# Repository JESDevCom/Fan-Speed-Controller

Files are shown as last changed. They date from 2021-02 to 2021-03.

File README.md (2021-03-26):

# Fan-Speed-Controller

**Part I. Introduction**
   * Re-Engineering a YLFC700 Fan Speed Controller (TRIAC based). This controller was originally sourced from an Xtrodinair Apex 42 Fireplace. The problem with the controller is that the slide potentiometer fails over time (about every 2-years). It fails at the slider's position where the fan runs just below max speed. 

**Part II. Theory for Failure**
   * The potentiometer is rated for 100[mW].
   * The reason the potentiometer fails is because the 47 [nF] Film capacitor begins to fail from transient voltage spikes after many startups.
   
**Part III. Testing Equipment Used**
1. Fluke 87V Digital Multimeter
2. Siglent SDS 1104X-E 100MHz Oscilloscope
3. Krohn-Hite Model 1600 3MHz Frequency Generator
4. Generic 5[V] 1[A] Fixed Power Supply
5. Hakko Soldering Station
6. Quick Hot Air Soldering Station

**Part IV. Software Used**
1. Windows 10 Pro
2. KiCAD 5.1
3. Matlab

**Part V. Parts Used**
1. RV1, 91A1A-B28-A22L, 0.2 [Ohms] to 250 [kOhms] Linear Potentiometer, Turn Knob Style, 2[W] max.
2. R1, 2.4k, Reused
3. R2, 270k, (Min: 0.25[W], Bought: 0.5[W])
4. R3, 18k,  (Min: 0.25[W], Bought: 0.5[W])
5. R4, 240k, (Min: 0.25[W], Bought: 0.5[W])
6. R5, 24, (Bought: 1[W])
7. U1, BTA16-600B, TRIAC (non-insulated tab package)
8. U2, DB3, DIAC (15 [uA] breakover current is my guess).
9. C3, 100 [nF], Film Capacitor 250[Vdc]
10. C2, 100[nF], Film Capacitor 250[Vdc]
11. C1, 47[nF], Ceramic Capacitor 1 [kVdc] (X7R)
12. L1, Inductor 7[uH] @ 1[KHz] (Measured with Scope, see characterization plot in Matlab folder)
13. 1/4" Dia. Metal Knob for Potentiometer

**Part VI. LTspice Simulation**
   * As the 47 [nF] fails, the potentiometer begins to seriously fall out of spec. 
   * Note, that the Power Factor (PF) is approximately 86% in the potentiometer resistance range where the slider fails (100 to 30k).

**Part VII. KiCAD Schematic**
   * Since this Controller adjusts the blower's speed on the fireplace and this motor is rated for 1.8 [A], let's design the PCB for double the max operating current because we can :). 
   * The only added components from the original design:
      1. 4 [A] fuse will be added, 
      2. a 24 [Ohm] resistor will be added in series with the potentionmeter since the potentiometer's minimum resistance is 0.2 [Ohms],
      3. a toggle switch to disconnect the controller from the 120 Volt mains to recreated the off detent that was on the original board, 
      4. and my design will not have any exposed PCB traces from the Fab.
      
   * We will reuse:
      1. 2.4k through-hole resistor,
      2. the two 100 [nF] film capacitors, 
      3. TRIAC, 
      4. DIAC, 
      5. and Inductor since these reactive components were engineered for use in the original design.

   * We will replace:
      1. 18k through-hole with a 18k in a 1206 package,
      2. 240k through-hole with a 240k in a 1206 package,
      3. 270k through-hole with a 270k in a 1206 package,
      4. the no-name slide potentiometer with a Bourns 91A1A-B28-A22L Knob Potentiometer,
      5. 47 [nF] 400 [Vdc] Radial Film Capacitor with a 47 [nF] 1 [kVdc] (X7R) Radial Ceramic Capacitor
     
   * A Bourns 91A1A-B28-A22L Knob Potentiometer (2[W], 0.2 to 250k [Ohms], linear) will repalce the original slide potentiometer (100[mW], 30 to 300k [Ohms], log). Since this potentiometer is in parallel with two other resistors, a 240k and 296k [ohms], the max resistance of the potentiometer doesn't matter that much. However, the minimum reistance does matter because it greatly affects the max speed (ie, the potentiometer controls the rate that the capacitors charge, which controls how the 120 [Vac] sinewave is chopped; thereby, changing the fan speed. marvelous).
   * Since the potentiometer goes down to 0.2 [Ohms], an excessive amount of current is drawn across the potentiometer, so a 24 Ohm resistor will be added in series with the potentiometer to approximately match the original slide potentiometer's minimum resistance. 
  
 **Part VIII. KiCAD PCB Design**
   * A two-side PCB will be created and fabricated, I used OSHpark as the frabricator.
   * SMD resistors for the 18k, 240k, 270k, 24 Ohm Resistors are required to make space for the Knob Potentiometer.
   * Certain traces that follow from the VAC input, to the TRIAC, and out to the motor must be fat traces (4mm) to stay below current and heat limits of having covered traces.
   * 0.2mm minimum distance between traces is important for 120[Vac] designs.

**Part IX. Disassembly of Original Boar & Removal of Components**
   * Remove the plastic & copper PCB mounting stands that connect the PCB to the metal outlet mount.
   * Use a Soldering Iron or Hot Air Station to remove the inductor, DIAC, TRIAC, and Capacitors.
   * Check capacitors with Fluke 87V.
   * Resolder the new and old components to the new board. 

**Part X. Results**
   * When removing the capacitors from the original board, the 47 [nF] Film Capacitor was measured at 1.2 [nF]. The 100 [nF] film capacitors were still in 10% spec.
   * After simulating the LTspice model with such a value (1.0nF) it became clear that the reason the potentiometer failed was because the 47 [nF] capacitor failed. This 47 [nF] capacitor is marked C1 on the original board (YLFC700).
   * Reason for failure: the capacitor is configured as a snubber and there is likely overvoltage spikes due to the motor.
   * Solution: Use a cermaic capacitor that has a higher maximum voltage rating that can withstand spikes resulting from the TRIAC switching. 
   
   * Successfully operating as of March 2021.

**Part XI. Legal Notice**
 
Under the MIT license to this project, you may use this design freely. An email to alledgedlyengineering @ gmail stating that you used this design would be nice to know. By using this project you are agreeing to the risks involved with AC current and altering a UL listed product to fit your needs. In addition, you agree to not hold me responsible for any injury or result of injury incurred by modifying the YLFC700 Fan Speed Controller. This project has no affliations with any of the manufacturers used in this design or the PCB fabrication house used.

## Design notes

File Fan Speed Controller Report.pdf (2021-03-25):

# YLFC700 Fan Speed Controller Product Failure & Solutions

## March 26, 2021

## John Schulz

# Table of Contents

Table of Contents | 1
Introduction | 3
Signs of Failure | 3
Theory for Failure | 3
Theoretical Design Flaws | 4
Specifications | 4
AC Motor | 4
YLFC700 | 5
Product Image | 5
Component List | 6
Fan Speed Controller (FSC) | 7
Component List | 7
Equipment Used | 8
Hardware | 8
Software | 8
Procedure | 8
Design | 9
YLFC700 | 9
Measured Inductor Characteristics | 11
LTspice Schematic | 11
Schematic Operation | 13
LTSpice Simulation | 13
Testing | 15
Transient Over Voltage | 15
Capacitor Measurements | 16
Solutions | 16
Fixing A New YLFC700 | 16
Engineering A Fan Speed Controller | 17
KiCAD Schematic | 17
KiCAD PCB Design | 18
Results | 21
Conclusion | 23
Appendix I - Code | 24

Inductor Characterization.m | 24
Power Factor.m | 28
LTspice Netlist | 29
Appendix II - Packaging | 32

# Introduction

The TRIAC-based fan speed controller used in an Xtrordinair Apex 42 fireplace has the model number: YLFC700. This unit is likely sourced by Travis Industries from an unknown supplier that produces the YLFC700. The fan speed controller is designed to control the speed of a single-pole 120V AC motor at a maximum AC current of 5A.

I own two units of the YLFC700, all of which have failed in the same manner. The problem with the controller is that the slide potentiometer partially fails over time, within 2 to 3 years, causing a specific range of usage on the potentiometer to no longer control the motor’s speed. To fix this problem I created my own personal hobbyist fan speed controller. I will call this version Fan Speed Controller (FSC) for the remainder of this document.

# Signs of Failure

Unfortunately, there are not any obvious signs that the unit begins to fail internally. The first external sign that the operator will notice is arcing across the contacts inside the slide potentiometer used in the YLFC700. The next sign of internal failure is when the contacts on the potentiometer become burnt out enough that contact can no longer be made and the motor stops operating in that position on the slide potentiometer. The slide range on the two YLFC700 units fail:
1. just below max speed (max speed still works) and
2. just above the halfway point on the slider.

# Theory for Failure

The potentiometer is likely rated to withstand 100mW of power. When a 120V AC current is applied and the controller is initially turned on, the potentiometer is its lowest resistance range which correlates to operating the motor at max speed. At this point, the transient state of the controller is affected by the inrush of current and a back EMF voltage spike from the motor initially receiving power from the controller. Inside the YLFC700, this transient voltage spike harms the 47nF 400V Film Capacitor C1, which in turn causes the 100mW potentiometer to fail as it is the next weakest link.

The reason capacitor C1 fails slowly is because a film capacitor is used and most film capacitors are self-healing. Since the transient condition that causes the failure only occurs at startup, the capacitor self-heals under normal operation; however, the self-healing characteristics degrade after each transient shock occurs. The reason the slide potentiometer only fails in the faster fan speed range of the controller is that this is the range of highest wattage consumed by the potentiometer.

# Theoretical Design Flaws

1. The YLFC700 does not use a snubberless TRIAC, yet the product was designed without a true snubber configuration being a resistor in series with C1. Due to the nature of the load (AC motor), the device should use a snubber to absorb the harsh opening and closing nature of the TRIAC.
2. Since the YLFC700 is designed to control motors, overvoltage transient protection using a TVS diode should probably be employed.
3. Depending on the load, a higher voltage-rated C1 capacitor may be a solution.
4. To reduce transient current inrush when the YLFC700 is turned on and connected to the AC motor, the slide potentiometer should be flipped 180 degrees to start the motor at its lowest speed instead of its highest speed.

# Specifications

The following specifications cover the motor that the YLFC700 is connected to, the components inside the YLFC700, and the components used in my hobbyist fan speed controller.

## AC Motor

Manufacturer: Fasco
Model Number (Type): U73B1 Voltage: 120V AC @ 60Hz
Current: 1.8A
Speed: 1550 RPM

In testing, the motor operated just below 1.8A when set at its max speed by the YLFC700 controller. This is normal and the motor ran as expected.

## YLFC700

### Product Image

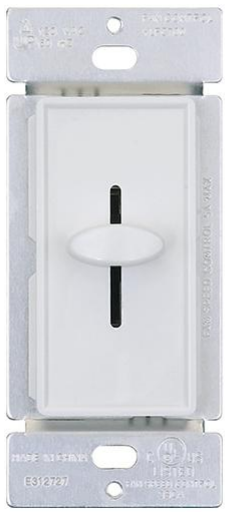
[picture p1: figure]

Figure 1 - YLFC700 OEM Product Image

The image in figure 1 displays the YLFC700 fan speed controller that is used in Travis Industries Apex 42 fireplace controller.

### Component List

Table 1 contains the list of components found inside the YLFC700 fan speed controller and the replacement components used in my hobbyist version.

Table 1 - YLFC700 Components
Original Components | Replacement Components (Hobbyist Version)
Slide Potentiometer, 20mm, 20-300k Ohms Logarithmic, 100mW | Rotary Potentiometer: RV1, 0.2-250k Ohms Linear, 2W
Resistor, 2.4k, Wattage NA | Resistor: R1, 2.4k*
Resistor, 270k, Wattage NA | Resistor: R2, 270k, 0.5 W
Resistor, 18k, Wattage NA | Resistor: R3, 18k, 0.5W
Resistor, 240k, Wattage NA | Resistor: R4, 240k, 0.5W
Film Capacitor: C1, 47nF, 400V | Ceramic Capacitor: C1, 47nF, 1kVdc (X7R)
Film Capacitor: C2, 100nF, 250V | Film Capacitor: C2, 100nF, 250V*
Film Capacitor: C3, 100nF, 250V | Film Capacitor: C3, 100nF, 250V*
TRIAC, BTA16-600B, non-insulated tab | TRIAC: U1, BTA16-600B, non-insulated tab*
DIAC, DB3, Breakdown Current NA | DIAC: D1, DB3, Breakdown Current NA*
Inductor: L1, Syle: Radial Vertical, Inductance Rating: Unknown, Measured at 7uH @ 1kHz | Reused Original Part*

* Components reused from the original PCB and resoldered to the new PCB board I created.

## Fan Speed Controller (FSC)

### Component List

Table 2 contains a list of components I used in my hobbyist version.

Table 2 - Fan Speed Controller v1.0 Components
Rotary Potentiometer: RV1, 0.2-250k Ohms Linear, 2W **

Resistor: R1, 2.4k *

Resistor: R2, 270k, 0.5 W **

Resistor: R3, 18k, 0.5W **

Resistor: R4, 240k, 0.5W **

Resistor: R5, 24, 1W ***

Ceramic Capacitor: C1, 47nF, 1kVdc (X7R) **

Film Capacitor: C2, 100nF, 250V *

Film Capacitor: C3, 100nF, 250V *

TRIAC: U1, BTA16-600B non-insulated, Style: Through-Hole *

DIAC: D1, DB3, Style: Through-Hole, Breakdown Current NA *

Inductor: L1, Style: Radial Verticle, Inductance Rating: Unknown, Measured at 7uH @ 1kHz *

¼” Dia. Metal Knob for Potentiometer ***

Fuse: F1, 4A Fast Blow. ***

* Components reused from the original PCB and resoldered to the new PCB board I created. ** Components different from the YLFC700 but serve the same purpose.
*** Components added to the circuit that was not in the YLFC700 circuit.

# Equipment Used

## Hardware

- Fluke 87V Digital Multimeter
- Siglent SDS 1104X-E 100MHz 4Ch Oscilloscope
- Krohn-Hite Model 1600 3MHz Frequency Generator
- Generic 5[V] 1[A] Fixed Power Supply
- Hakko Soldering Station
- Quick Hot Air Soldering Station

## Software

- Windows 10
- KiCAD 5.1
- Matlab 2017

# Procedure

The following steps are the procedure followed when re-engineering the YLFC700 while searching for the probable cause of failure.

1. Use the original PCB inside the YLFC700 to draw the schematic out in LTspice
2. Check resistor and capacitor values with Fluke 87V
3. Measure the inductor value with a frequency generator and Siglent oscilloscope
4. Record inductor values in Matlab and plot inductor characteristic curves
5. Calculate the power factor of the LTspice circuit to check if the potentiometer is within power spec
6. Draw schematic in KiCAD
7. Design PCB in KiCAD
8. Send PCB design to OSHpark for fabrication
9. Transfers reusable components from YLFC700 to FSC
10. Test motor with FSC and AC power source

# Design

## YLFC700

The construction of the YLFC700 PCB is a one-sided board that uses all through-hole mounted components.

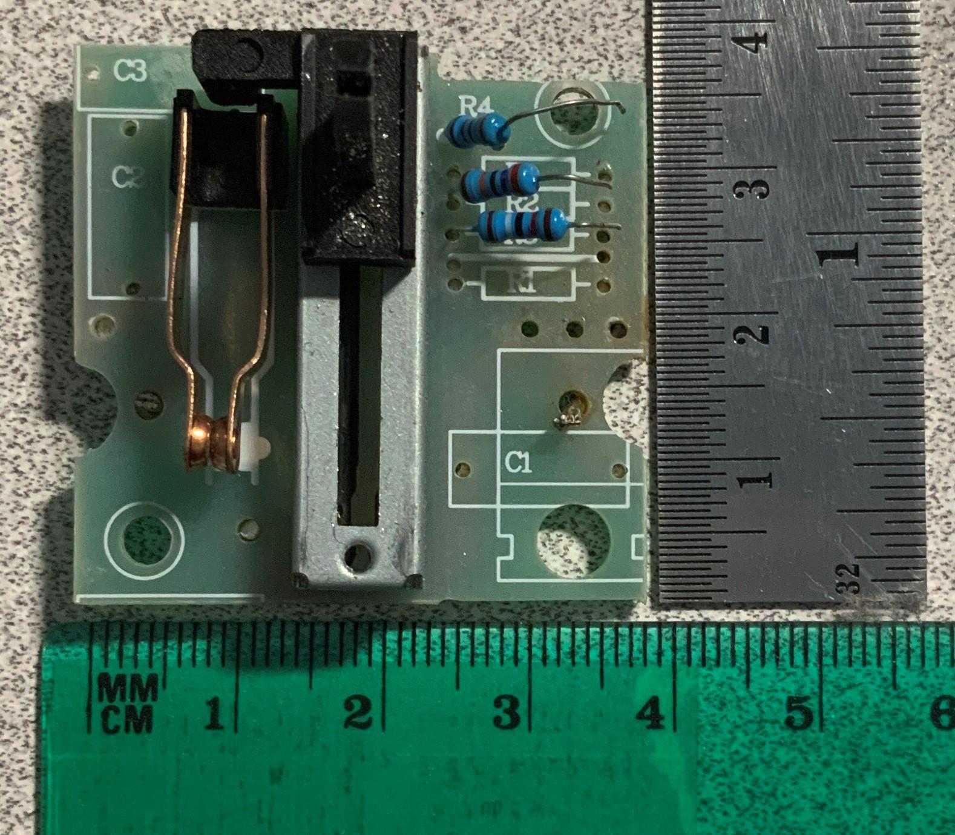
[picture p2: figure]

Figure 2 - YLFC700 PCB Front Side View

Figure 2 depicts an image of the PCB’s front side. This is the side of the board that faces the user when operating the fan controller. Some components have been removed from the board for the purpose of measuring their values. The removed components are as followed: C1, C2, C3, L1, TRIAC, DIAC, and R1. The dimensions of the PCB are 38mm along the translucent green ruler and 37mm along the metal silver ruler.

The long component located in the center of the board is the logarithmic slide potentiometer. The potentiometer has a slide distance of 20mm, a knob height of 20 mm, and dimensions of 35mm x 8.3mm x 6mm (L x W x H). The potentiometer is mounted to the board by 4 through-hole pins, two of which are necessary for operation. The pitch between the potentiometer’s pins is 3.5mm. Through research, I think this potentiometer is made by Panasonic and is rated for 100mW. Unfortunately, Panasonic no longer produces this exact potentiometer.

Next, the copper clip to the left of the slider is the power disconnect switch. The user feels this switch as a detent when turning off the controller.

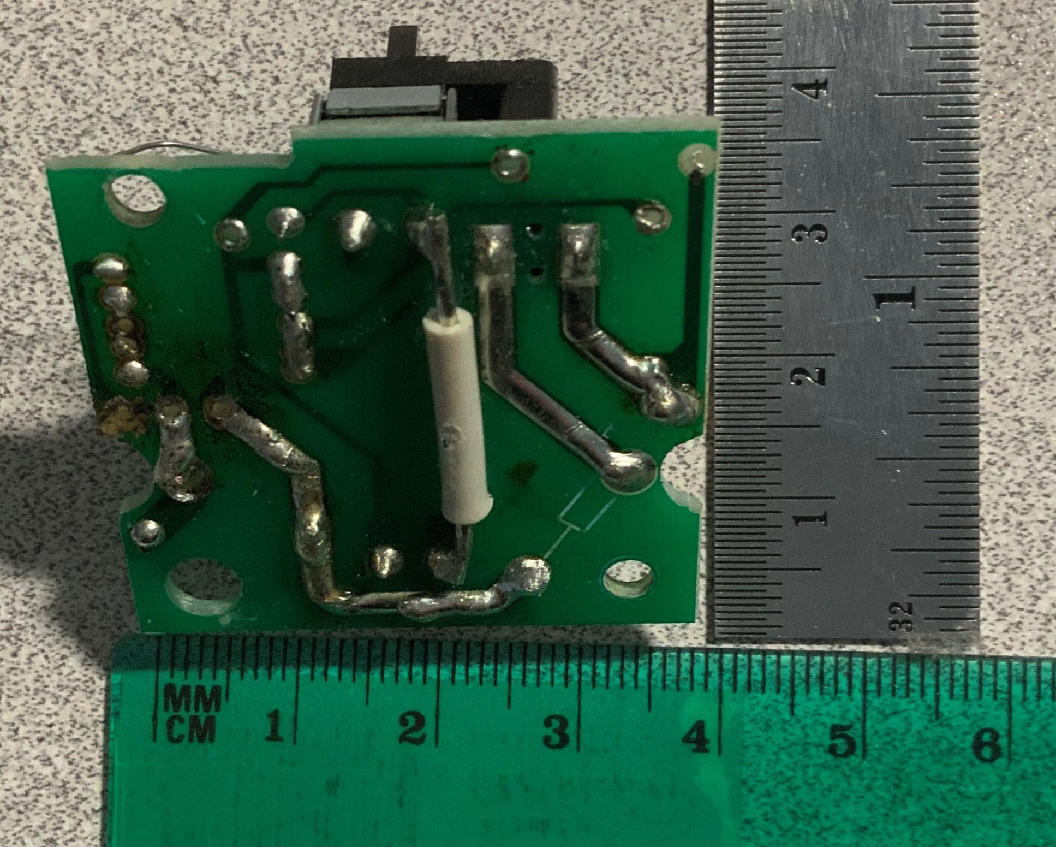
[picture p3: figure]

Figure 3 - YLFC700 PCB Back Side View

Figure 3 shows a view of the backside of the board, which is the side of the board that faces the wall when the user is operating the fan controller. Open traces were used along the main power route from the mains power side through the inductor, TRIAC, and out to the motor. Using exposed traces is a cheap way to carry a lot of current while dissipating heat. The black ABS plastic shielding that covers the PCB on the backside of the YLFC700 is required to shield the open traces.

### Measured Inductor Characteristics

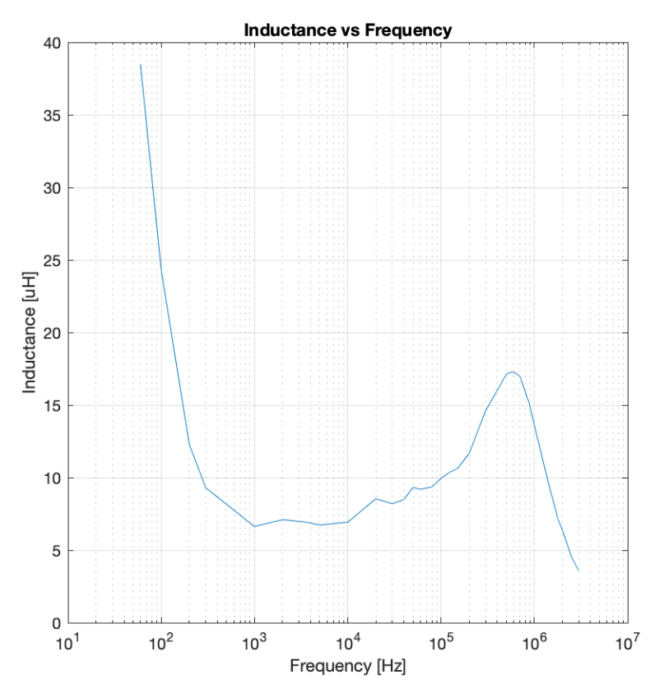
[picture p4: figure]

Figure 4 - Inductor (L1) Inductance vs Frequency

The inductor characteristics, shown in figure 4, used data collected and saved in a Matlab script to plot the above inductance versus frequency curve. The first point in the plot was collected at 60 Hz, which is the frequency the inductor will be operating at inside the YLFC700. Hence, an inductance value of 37uH will be used in the following LTspice simulations. See Appendix I, for the full Matlab characterization script with data.

### LTspice Schematic

After measuring the discrete components and sketching the PCB traces, the following schematic was created in LTspice. To simplify simulating an AC motor, an inductor in series with a resistor was implemented. It is my assumption that the motor would be relatively close to the value of the inductor L1 so 47uH was chosen. Secondly, the resistor value for R6 was chosen such that the motor would draw 1.8A when the potentiometer is set to operate the motor at max RPM. Note, all simulations use a 120V 60Hz sine wave input.

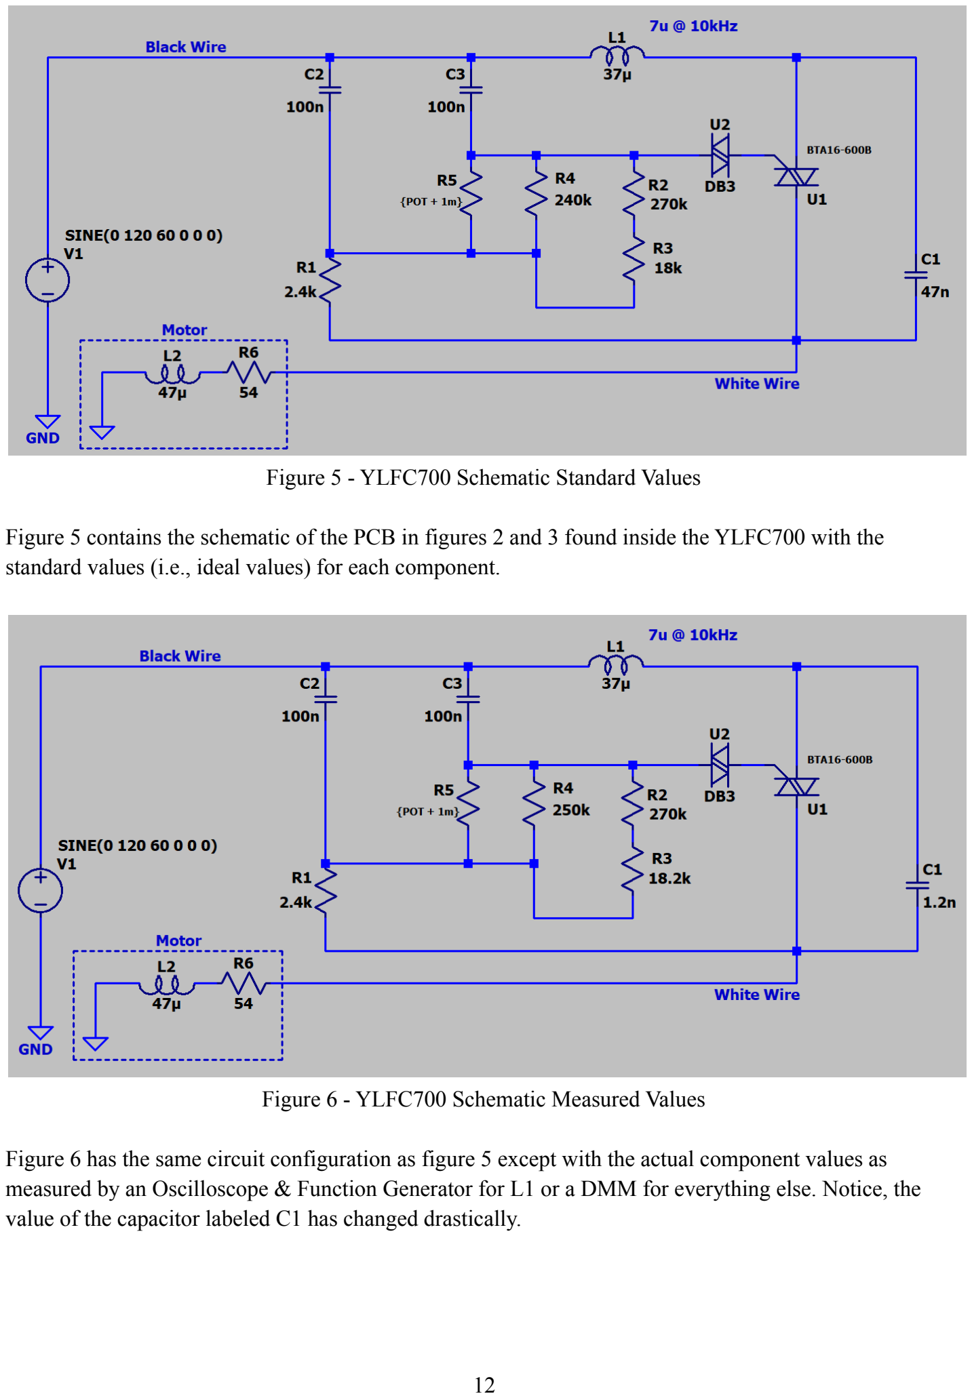
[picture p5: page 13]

Figure 5 - YLFC700 Schematic Standard Values

Figure 5 contains the schematic of the PCB in figures 2 and 3 found inside the YLFC700 with the standard values (i.e., ideal values) for each component.

Figure 6 - YLFC700 Schematic Measured Values

Figure 6 has the same circuit configuration as figure 5 except with the actual component values as measured by an Oscilloscope & Function Generator for L1 or a DMM for everything else. Notice, the value of the capacitor labeled C1 has changed drastically.

### Schematic Operation

To break down the operation of the circuit from the schematic in figures 5 and 6, let's first discuss the DIAC and TRIAC (labeled U2 and U1). Under normal operation, the TRIAC opens and closes allowing current to flow through when a specific voltage is met at its gate. The DIAC controls the TRAIC’s gate. The DIAC turns on allowing current to flow through once a specific breakdown current occurs inside the DIAC. This breakdown current event can only occur once the capacitors C2 and C3 are charged. Hence by adjusting the rate at which C2 and C3 charge using the resistor network R1-5, the user can control DIAC.

The RPM of the AC motor is controlled by chopping the sine wave input; whereby, the motor does not see the full length of the sine wave over each period which manipulates the speed. The inductor L1 operates as an inductive line choke to keep the noise from the motor out of the mains. L1 and C1 are used to absorb the voltage spike caused by the motor when the TRIAC closes. Also, the capacitor C1 is used to fill the load when the TRIAC first opens; thereby, reducing the inrush current pulled from the mains.

Note, that if a resistor had been placed in series with C1, this part of the circuit would be a true snubber configuration.

### LTSpice Simulation

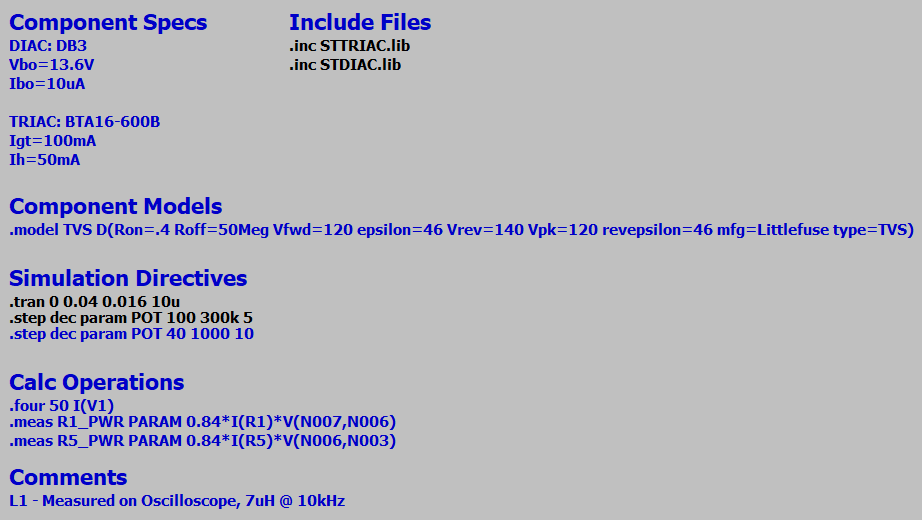
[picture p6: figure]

Figure 7 - LTspice Operations

The Spice operations used to simulate figures 5 through 6 are shown above in figure 7. Since the exact spice libraries for the DIAC and TRIAC used in the YLFC700 do not come with LTspice, one must download the files from STMicroelectronics and tell LTspice to include them. The circuits are simulated from 16ms to 40ms with a maximum timestep of 10us. The circuit has reached steady-state by 16ms. For each time simulation, a different potentiometer value is used in a logarithmic step from 100 Ohms to 300 kOhms with 5 points per decade.

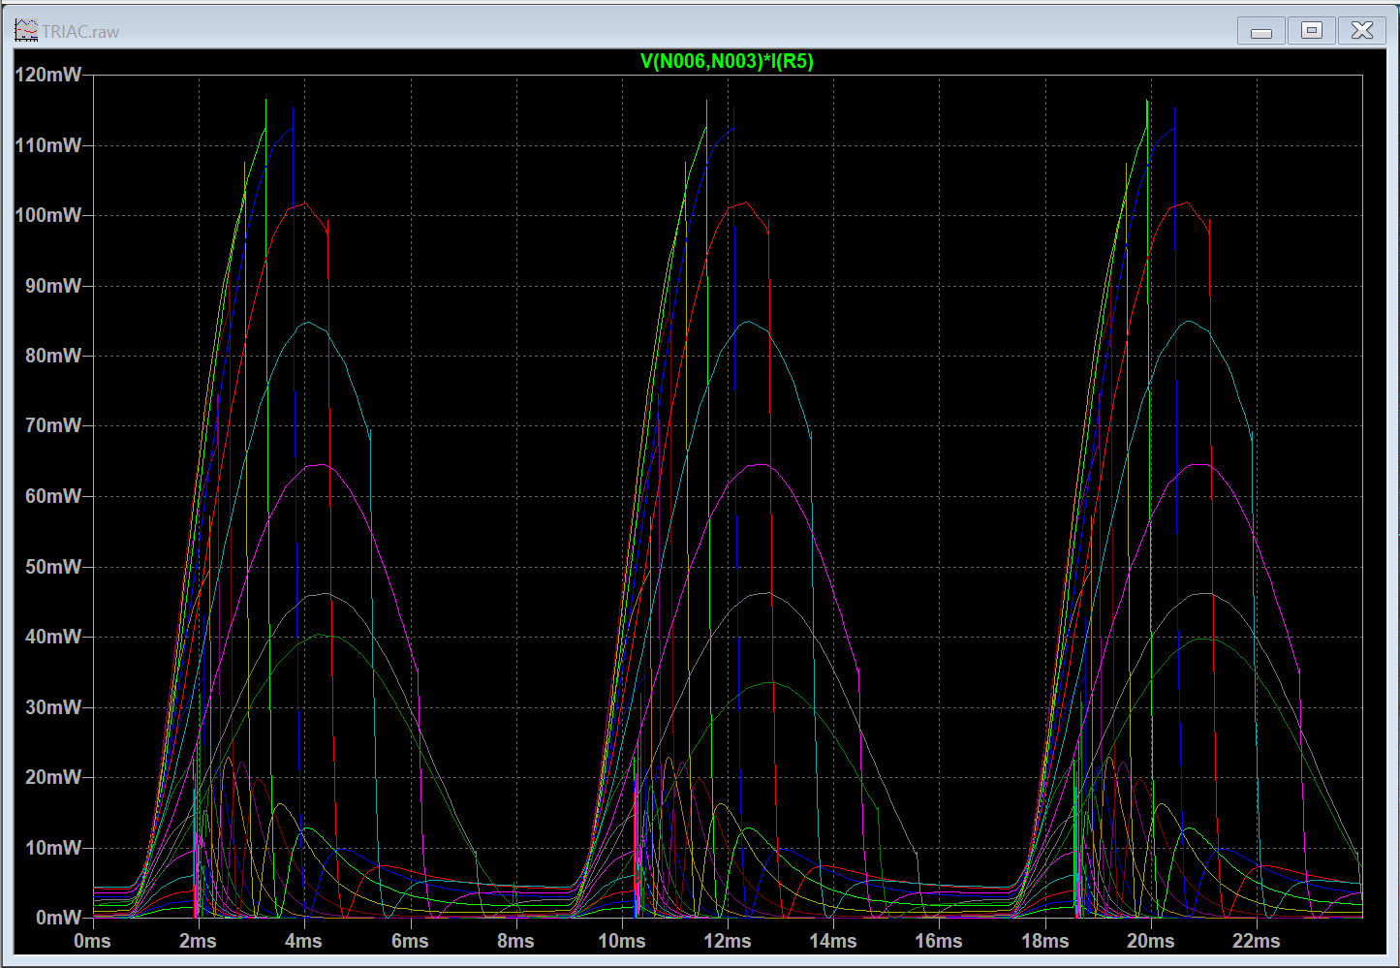
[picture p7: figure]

Figure 8 - Potentiometer Power Using Standard Values

To produce the simulation shown in figure 8, the circuit in figure 5 (actual values) and the operations in figure 7 are applied. When considering a power factor of approximately 86% for the potentiometer’s resistance values between 100 and 30,000 Ohms, the above results would be within specification. See Appendix I, for the Matlab script containing the power factor data collected from running the .four 50 I(V1) command in LTspice.

So, what happens when C1 starts to fail?

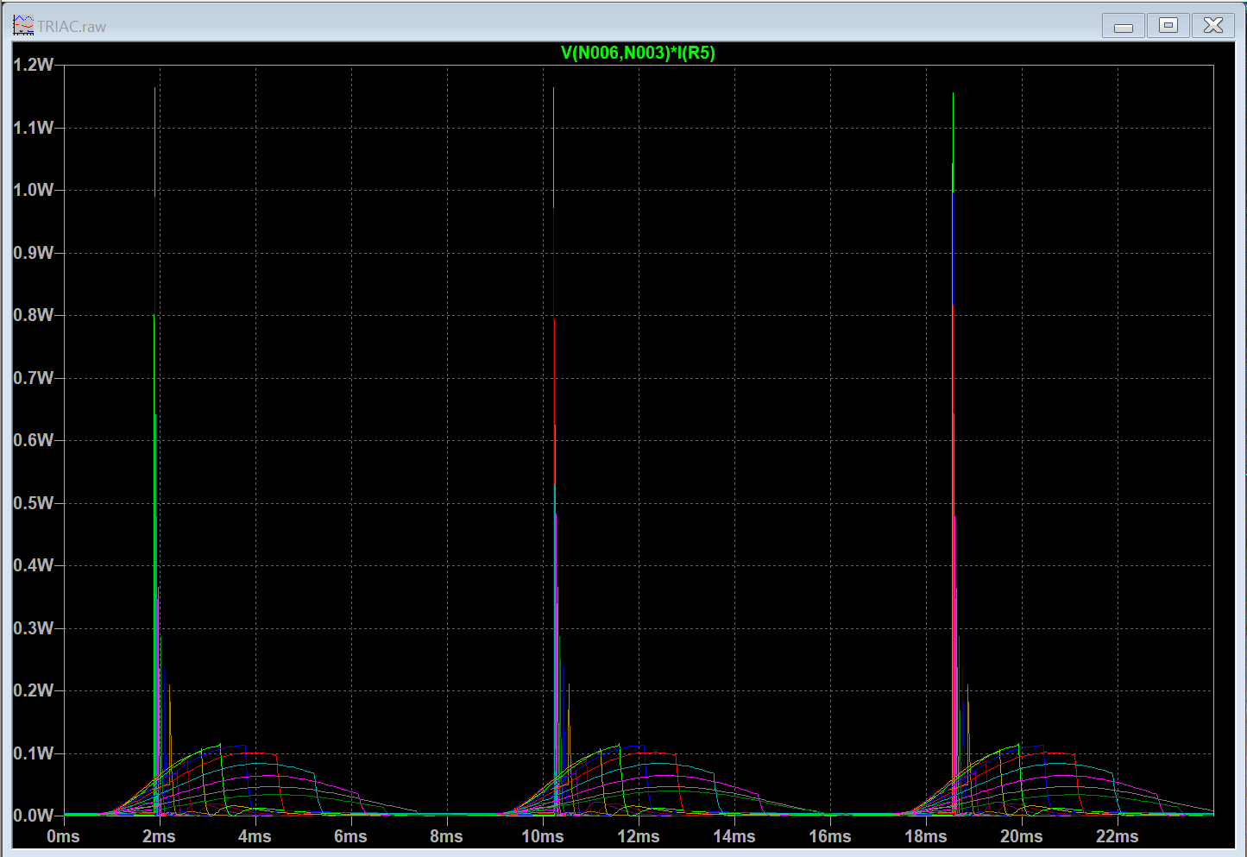
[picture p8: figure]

Figure 9 - Potentiometer Power Using Measured Values

To produce the simulation shown in figure 9, the circuit in figure 6 (measured values) and the operations in figure 7 are applied. Now one can see that when C1 fails and its capacitance decreases, the potentiometer falls dramatically out of specification over a range of resistance values from 100 to 30,000 Ohms. Hence, this is why the potentiometer inside the YLFC700 fails only in the upper-speed range, while the lower-speed control range remains functional.

# Testing

## Transient Over Voltage

During testing of the YLFC700 design, a transient voltage spike was seen when turning the unit on. I made an error in using my Oscilloscope without a high voltage differential probe. I was rather scared that I had ruined something inside my scope and I forgot to take a screenshot of the transient voltage spike. My probes were set at x10, my scope has a max peak to peak voltage of 400V, and my vertical V/div was set at the scope’s maximum. Under these conditions, I was unable to see the peak of the spike and I had my trigger set at 200V; therefore, I am assuming that the spike is around 400 volts or greater. Hence, the conditions would be met for the 400V rated capacitor to fail slowly.

## Capacitor Measurements

Capacitor C1 was measured before and after removal from the PCB. For both measurements, C1 was measured to be 1.2nF. Capacitors C2 & C3 were measured at 100nF.

# Solutions

There are two approaches to fixing the design flaws of the YLFC700:
1. Fix a brand new YLFC700 unit, or
2. Build a new fan speed controller.

## Fixing A New YLFC700

To fix a brand new YLFC700, place a Transient Voltage Suppression (TVS) diode on the right side of the circuit in parallel with C1, as seen in the figure below. This addition will protect C1 from the transient voltage spike cause when starting the motor.

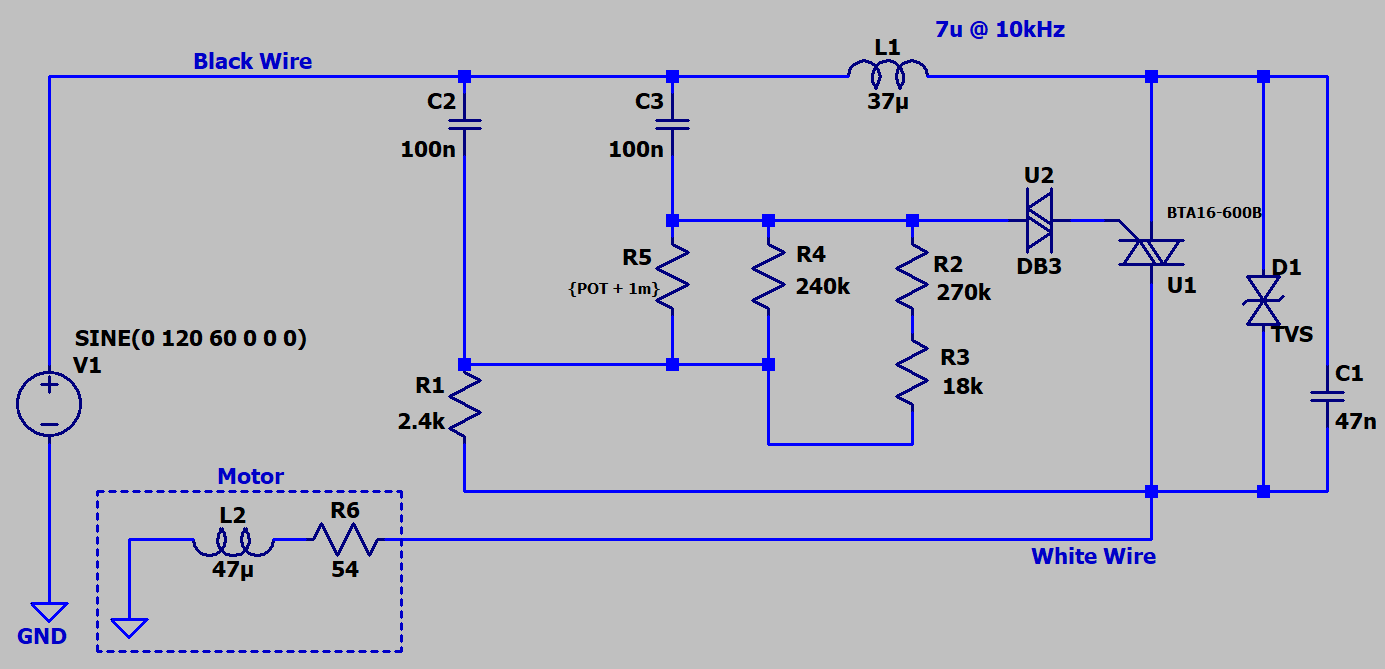
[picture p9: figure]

Figure 10 - Adding Transient Voltage Protection

A TVS diode such as the 5KP220CA by Littlefuse would be a good component for this problem since it will keep C1 from seeing a voltage greater than +/- 371V. Luckily, there is room to add a TVS diode to the YLFC700.

## Engineering A Fan Speed Controller

There are a few design considerations I made when re-engineering the circuit.
1. We want to reuse the original TRIAC mounted to the metal installation wall bracket along with the black ABS plastic cover used on the YLFC700; therefore, our new circuit board must fit inside the existing housing. See figure 17 as an example.
2. We may want to add a heftier wattage potentiometer than necessary. Slide potentiometers do not exist in a 2W package under our design constraints, so a rotary potentiometer will be used. A resistor (R5) must be added in series with the potentiometer to match the minimum resistance of the original slide potentiometer. This is necessary for the potentiometer chosen for our design because its minimum resistance is 0.2 Ohms.
3. A toggle switch (SW1) will be added to emulate the detent in the YLFC700 to disconnect the controller from the mains.
4. It never hurts to add a fuse, so a 4 Amp fuse will be added.
5. A 1kV ceramic capacitor will be used to replace the 400V film capacitor (C1). The ceramic cap will be much smaller than the film capacitor and it will fit better in the design.

Note: A film capacitor would still fit. Ceramic capacitors do not have self-healing properties like film capacitors; however, since our 600V rated TRIAC is not failing, I am assuming that a 1000V capacitor will survive.

### KiCAD Schematic

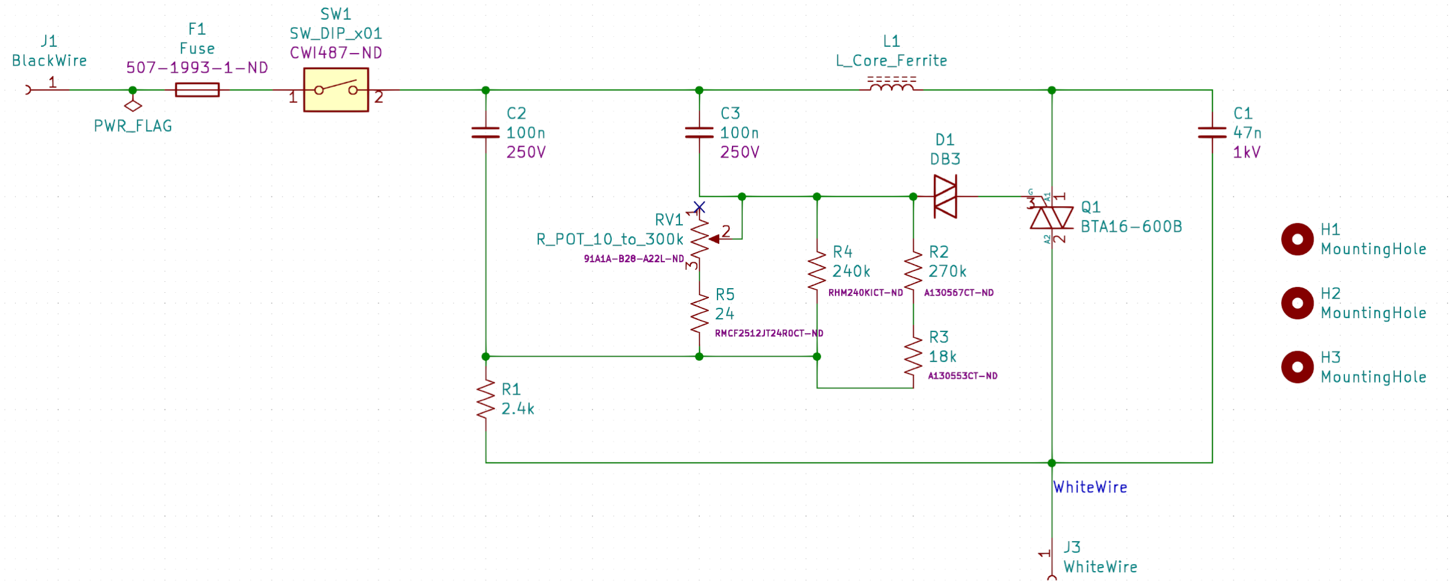
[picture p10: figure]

Figure 11 - KiCAD Schematic

Figure 11 shows the modified circuit that is used in my Fan Speed Controller design. The wire colors used on the YLFC700 correspond to the labels used in the above schematic. Notice, the original PCB had 3 mounting holes that were of different sizes and not connected to any traces on the board.

### KiCAD PCB Design

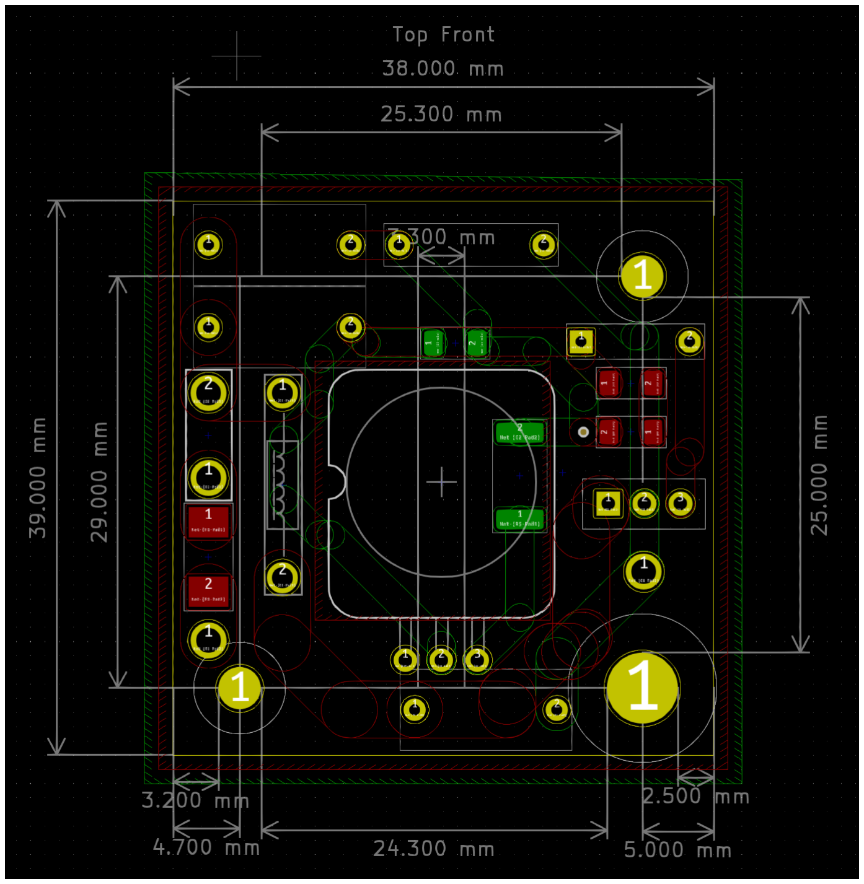
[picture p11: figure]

Figure 12 - KiCAD Design

Figure 12 shows the dimensions and spacing of components on the board. The diameter of the mounting holes and spacing between the mounting holes is critical if we want to reuse the existing YLFC700 mounting bracket and ABS plastic back cover. To add additional room for components, the height of the board increased by 2mm along its y-axis.

The yellow outline around the board marks the cut line that the fabricator will follow when they CNC our board. The red and green outline around the yellow cut line marks where the soldering mask will be poured. These two red and green boxes can be arbitrarily set anywhere outside the yellow cut line. Note, that the solder mask will be excluded from the top red layer, behind the potentiometer. This extra measure was implemented in the event that the potentiometer wiggles and wears on the PCB face to keep the potentiometer from ever touching the top layer traces. This should never occur under normal circumstances, but at the time of the KiCAD design, I didn’t know how snuggly the unit would go together.

Different trace widths were used in various areas of the design. By my estimation, the exposed traces on the original YLFC700 PCB were meant to handle a sustained 16A along the main route from the power input to the motor. However, we know our load uses a max 1.8AAC.

Using the Track Width PCB calculator in KiCAD, and knowing our fabricator will be OSHpark which uses a trace thickness of 0.0356mm, we can calculate the necessary trace thickness to handle the currents we expect using the IPC 2221 standard.

Thus, a 4mm wide internal trace with a temperature rise of 80C will allow the circuit to handle a max current of 8.25A along the main power trace from the 120V AC power input to the load. Similarly, a 2mm wide internal trace will handle 5A. This design uses either 4mm or 2mm traces because it is better to have extra thermal dissipation overhead than less. Considering the high voltage within this circuit and the transient voltage spike issue, a 0.2 mm space between traces was implemented for safe operation at high altitudes.

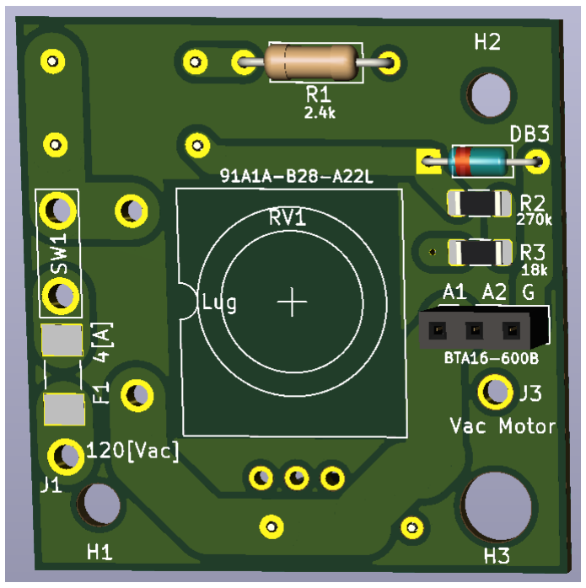
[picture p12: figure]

Figure 13 - KiCAD PCB 3D Rendering Front Side

Figure 13 shows the other side of the PCB depicted in the previous figure. This view clearly shows the difference in drill hole sizes and through-hole sizes. Note, the drill holes labeled H1 and H2 are the same in size at 3mm in diameter and H3 is 5mm in diameter. The through-holes for the 120[Vac] power input, switch (SW1), and Vac Motor are all 1.5mm in diameter to handle the larger gauge wires necessary for operation. The potentiometer’s rotary shaft is placed at the center of the PCB.

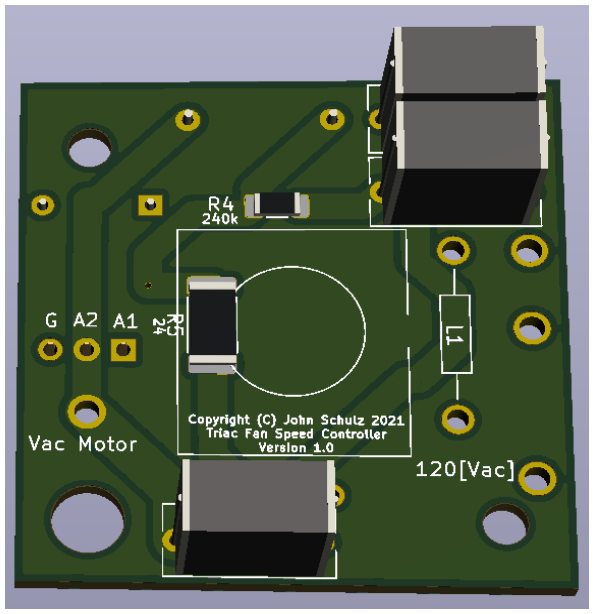
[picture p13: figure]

Figure 14 - KiCAD PCB 3D Rendering Back Side

Figure 14 depicts a 3D rendering of the backside of the design shown in figure 13. The capacitors are represented by the large brick objects on the board. The three legs of the TRIAC are clearly marked by the labels: Gate, A2, and A1.

# Results

All reusable components were removed with a soldering iron, except for the TRIAC. The TRIAC required a hot air station and some pliers of persuasion to desolder the 3 leads without damaging them.

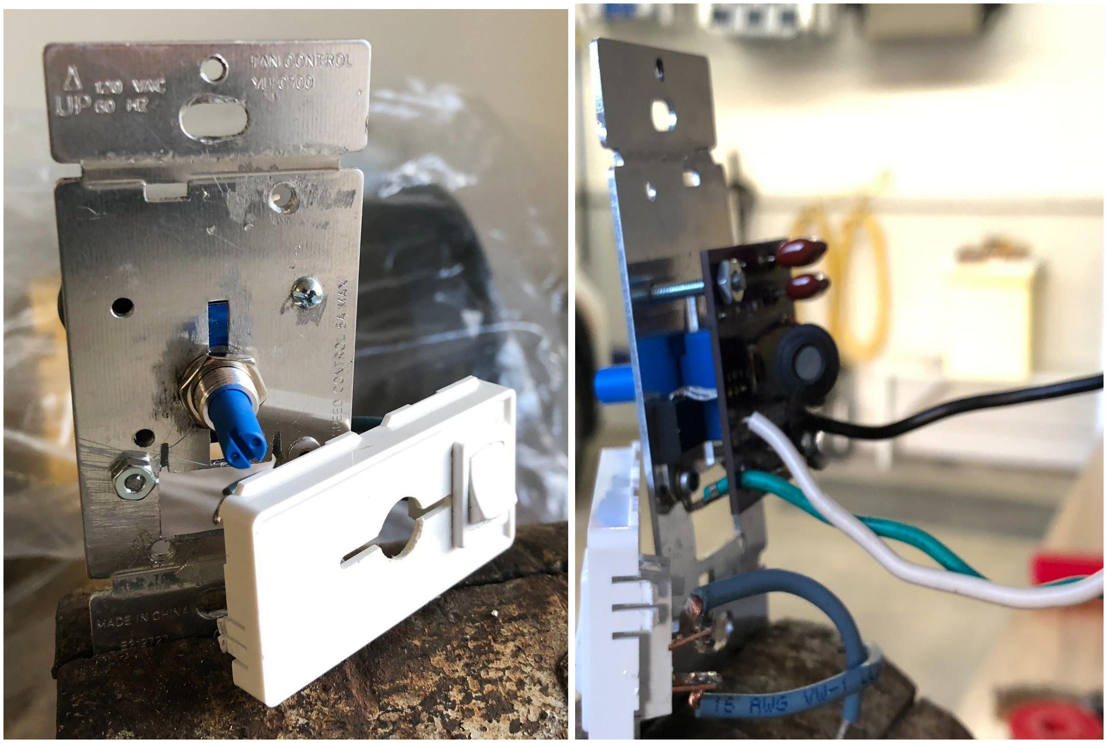
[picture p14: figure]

Figure 15 - FSC Disassembled Front Side | Figure 16 - FSC Disassembled Back Side

Figure 15 shows the front side of the Fan Speed Controller (FSC) without the white front plastic covering and the modifications made to the metal mounting bracket. A Dremel, file, and battery drill were used to make the modifications seen in figures 15 and 16.

The PCB was mounted using screws from a hardware store that are shown in figure 16. Although not visible in figure 16, a rubber shield made from electrical wire heat shrink is used to shield the head of the screw in hole H1 from ever contacting the wire inserted at hole J1. This is extra protection in the event of rubbing. Under the intended operating environment, contact should never be made.

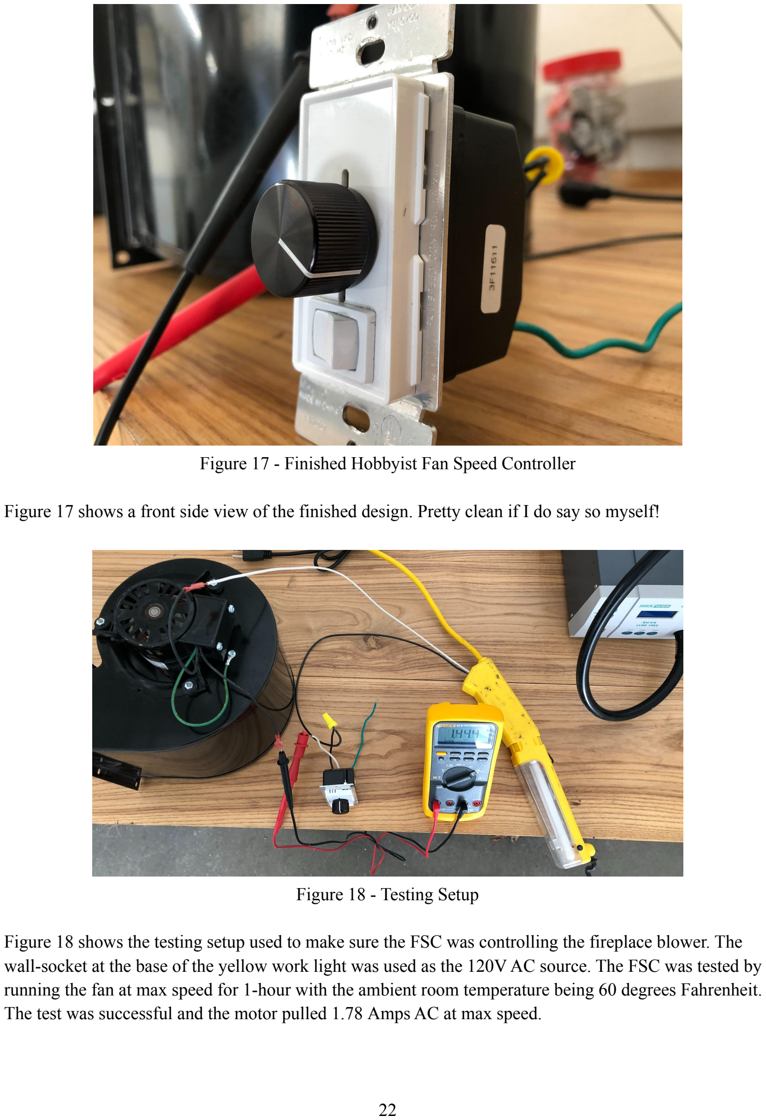
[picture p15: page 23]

Figure 17 - Finished Hobbyist Fan Speed Controller

Figure 17 shows a front side view of the finished design. Pretty clean if I do say so myself!

Figure 18 - Testing Setup

Figure 18 shows the testing setup used to make sure the FSC was controlling the fireplace blower. The wall-socket at the base of the yellow work light was used as the 120V AC source. The FSC was tested by running the fan at max speed for 1-hour with the ambient room temperature being 60 degrees Fahrenheit. The test was successful and the motor pulled 1.78 Amps AC at max speed.

# Conclusion

- Capacitor C1 inside the YLFC700 is failing, likely due to a transient voltage spike at startup.
- Potentiometer fails in a specific resistance range as a result of C1 failing.
- The overvoltage issue can be addressed in several ways: TVS diode, higher voltage rated C1, or making the potentiometer start at its maximum resistance upon startup.

# Appendix I - Code

## Inductor Characterization.m

The following Matlab code uses logged values to plot the inductor (L1) characterization curves.

%{
Creator: AlledgedEngineering
Date: 2/7/2021
Tile: Inductor Characterization
Description: Plot recorded value to characterize an inductor used in a TRIAC circuit for AC Motor Speed Control.

Equipment:
Oscilloscope: Siglent SDS1104X-E 100MHz 4Ch
Frequency Generator: Krohn-hite Model 1600 3MHz DMM: Fluke 87V

Signal:
Sinewave with 10[Vpp]

Circuit:

Function Generator
| | 50 Ohm | | | Rref | Va2
| | .---^^^^-------*---^^^^^---*
| | | | | Va1 | |
| | | | | | >
| (~) Vin | | | > Resr
| | | | | | >
| | | | | | &
| | | | | | & L
| | | | | | &
| | '---------------- GND -----'
'-----------------'
%}
clc
clear all

% DC Resistance
Vdc = 4.983; % Volts
Idc = 0.567; % Amps
Rdc = Vdc/Idc;
fprintf('DC Resistance: %0.2f [V]\n', Rdc);

% Reference Resistor
Rref = 99.9; % ohms
fprintf('Reference Resistor: %0.1f [Ohms]\n', Rref);

% Data Points Collected
Va1 = [9.8, 10, 10.2, 10.0, 10, 10, 10, 10, 10, 10, 10, 10.2, 10.2, 10.2, 10.2, 10.2, 10.2, 10.2, 10.4 10.4, 10.4, 10.8, 11, 11.2, 11.4, 11.6, 12.2, 12.6, 13.6, 13.8, 14.4, 14.6, 15.4, 15.8]; % Volts
Va2 = [0.004, 0.0044, 0.0044, 0.0052, 0.0132, 0.0276, 0.0464, 0.0648, 0.1072, 0.1314, 0.246, 0.372, 0.472, 0.596, 0.704, 0.904, 1.12, 1.38, 1.62, 2.12, 3.18, 4.16, 5.04, 5.52, 6, 6.8, 8.08, 8.88, 10.88, 11.2, 12.16, 12.72, 13.4, 13.6]; % Volts theta=[92.5, 92, 92.7, 91.4, 90.1, -89.5, -89.2, -89.4, -89.5,-89.23, -83.11, -84.2, -82.2, -80.1, -80.4, -79.3, -77.75, -76.7, -75.2, -72.8, -67.4, -63.1, -57.2, -56.6, -54.7, -50.2, -45, -40.6, -30.3, -28.6, -21.5, -19.4, -10, -6]+90; % Deg
freq =[60, 100, 200, 300, 1000, 2000, 3500, 5000, 8100, 10000, 20000, 30000, 40000, 50000, 60000,80000, 100000, 125000, 150000, 200000, 300000, 400000, 500000, 550000 604000, 700000, 876639, 1*10^6, 1.41*10^6, 1.5*10^6, 1.8*10^6, 2.01*10^6, 2.5*10^6, 3*10^6]; % Hz

% Impedance [Ohms]
z = Va2*Rref ./ sqrt( (Va1.^2) - 2 * Va1 .* Va2 .* cosd(theta) + Va2.^2); [val,indx] = max(z);
fprintf('Resonance Frequency: %.1f [kHz]\n', freq(indx)*10^-3);

% Angle of Impedance [Degrees]
angle = theta - atand(-1*Va2.*sind(theta)/ (Va1-Va2.*cosd(theta)));

% Now we can convert to rectangular form ZZ of the impedance to find the % resistance and capacitance.
% | Z = Resr + j*X
% | => Resr + j*2*pi*freq*L
% | => Z*cos(angle) + j*Z*sin(angle) %}

Resr = z .* cosd(angle);
L = z.*sind(angle) ./ (2 * pi * freq);

% Inductive Reactance
X = 2*pi.*freq.*L;

figure(1)
subplot 231
semilogx(freq, z), grid on;
xlabel('Frequency [Hz]'), ylabel('Impedance [Ohms]'); title('Inductor Impedance');

subplot 232
semilogx(freq, angle), grid on;
xlabel('Frequency [Hz]'), ylabel('Phase [deg]'); title('Angle of Impedance');

subplot 233
semilogx(freq, abs(L*10^6)), grid on; xlabel('Frequency [Hz]'), ylabel('Inductance [uH]'); title('Inductance vs Frequency');

subplot 234 semilogx(freq, Resr), grid on; xlabel('Frequency [Hz]'), ylabel('Resr [Ohms]'); title('Resr vs Frequency');

subplot 235
semilogx(freq, X), grid on;
xlabel('Frequency [Hz]'), ylabel('Inductive Reactance [Ohms]'); title('Reactance X_L vs Frequency');

subplot 236
semilogx(freq, (Va1-Va2)./Rref), grid on
xlabel('Frequency [Hz]'), ylabel('Current [A]'); title('Current over Rref');

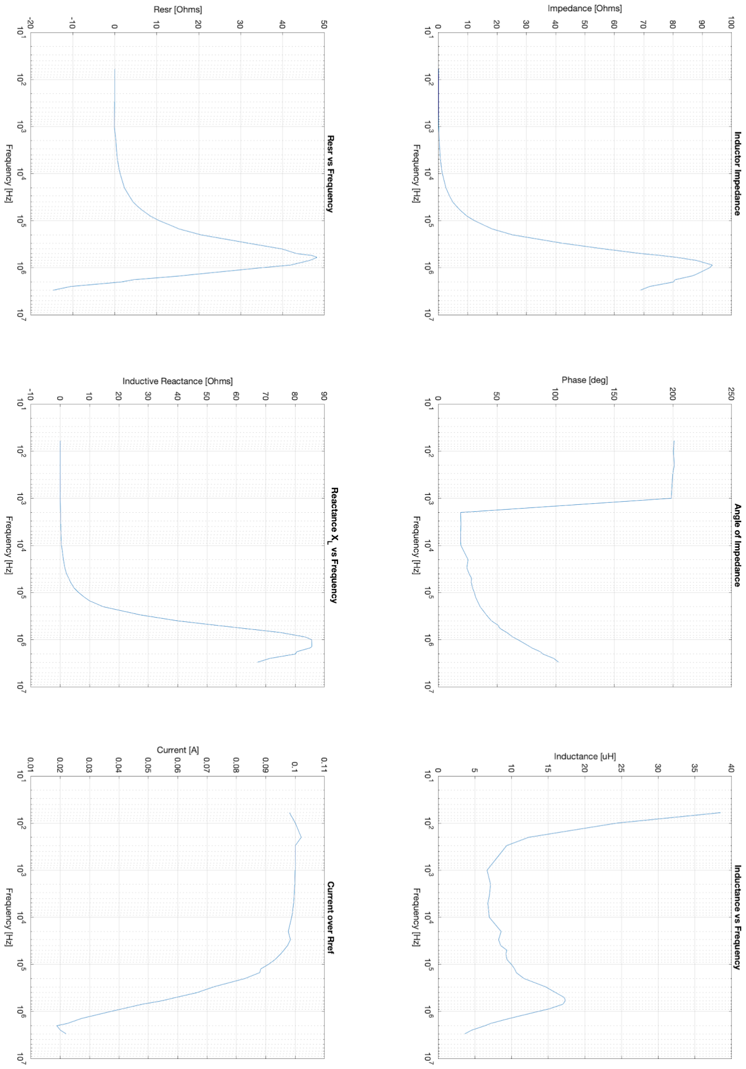
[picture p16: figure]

Figure 19 - Full Inductor Characterization Plots

## Power Factor.m

%{
Creator: AlledgedEngineering
Date: 3/20/2021
Tile: Inductor Characterization
Description: Plot recorded value of the power factor at different potentiometer resistance amounts.
Collect values from LTspice.

%}
clc
clear all

% Data Points Collected
Rpot = [100, 158.5, 251.19, 398.1, 631, 1000, 1584.89, 2511.89, 3981.07, 6309.6, 10000, 15849, 25119, 39810, 63095, 100000, 158489, 251189, 300000]; % Potentiometer Resistance
PF = [0.8421, 0.8423, 0.8426, 0.8431, 0.8438, 0.8422, 0.8466, 0.8493, 0.8500, 0.8555, 0.8674, 0.8728, 0.8922, 0.9065, 0.8940, 0.8174, 0.6967, 0.4625, 0.4921]; % Power Factor

figure(1)
plot(Rpot, PF), grid on;
xlabel('Potentiometer Resistance [Ohms]'), ylabel('Power Factor'); title('Power Factor vs Potentiometer Resistance');

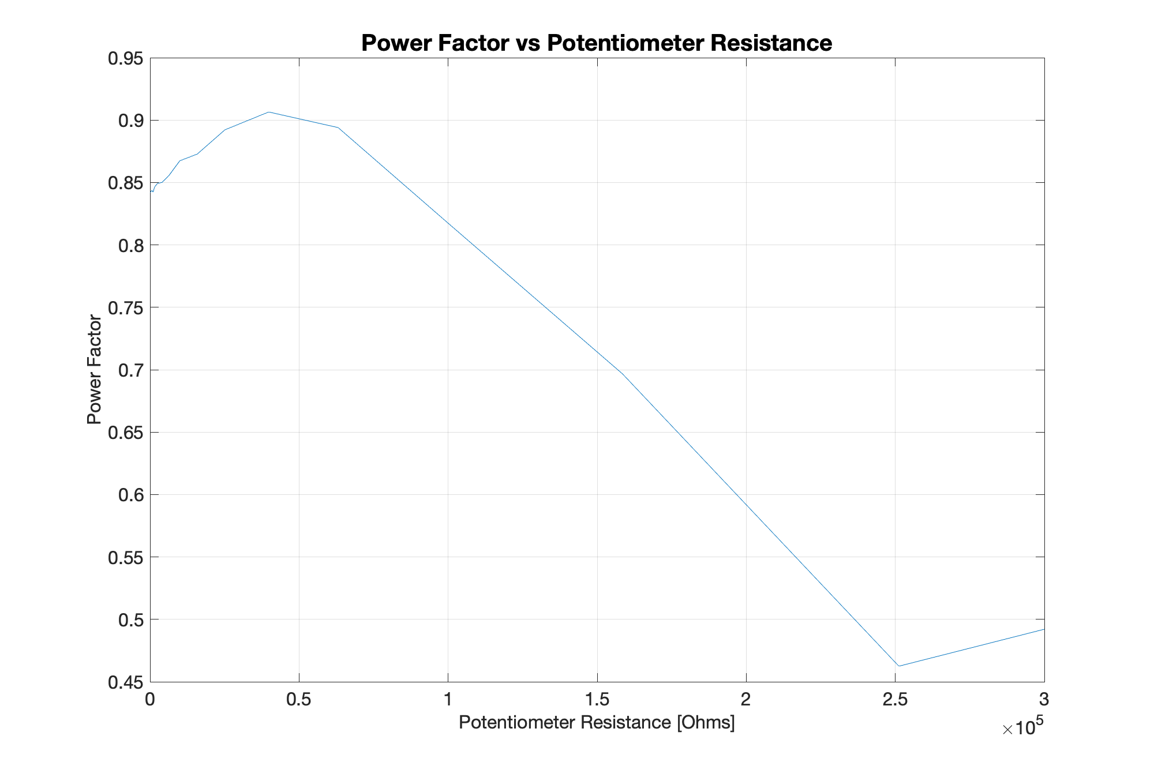
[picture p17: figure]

Figure 20 - Power Factor LTspice Data Plot

## LTspice Netlist

Version 4
SHEET 1 1120 680
WIRE -560 -240 -976 -240
WIRE -352 -240 -560 -240
WIRE -176 -240 -352 -240
WIRE 128 -240 -96 -240
WIRE 304 -240 128 -240
WIRE -560 -224 -560 -240
WIRE -352 -224 -352 -240
WIRE -352 -96 -352 -160
WIRE -256 -96 -352 -96
WIRE -112 -96 -256 -96
WIRE -16 -96 -112 -96
WIRE 80 -96 48 -96
WIRE 128 -96 128 -240
WIRE -352 -80 -352 -96
WIRE -256 -80 -256 -96
WIRE -112 -80 -112 -96
WIRE -112 16 -112 0
WIRE -976 48 -976 -240
WIRE -560 48 -560 -160
WIRE -352 48 -352 0
WIRE -352 48 -560 48
WIRE -256 48 -256 0
WIRE -256 48 -352 48
WIRE 304 48 304 -240
WIRE -256 128 -256 48
WIRE -112 128 -112 96
WIRE -112 128 -256 128
WIRE -560 176 -560 128
WIRE 128 176 128 -32
WIRE 128 176 -560 176
WIRE 304 176 304 112
WIRE 304 176 128 176
WIRE -832 224 -896 224
WIRE -720 224 -752 224
WIRE 128 224 128 176
WIRE 128 224 -640 224
WIRE -976 288 -976 128
WIRE -896 304 -896 224
FLAG -976 288 0
FLAG -896 304 0
SYMBOL voltage -976 32 R0
WINDOW 123 24 124 Left 2
WINDOW 39 0 0 Left 0
WINDOW 3 -299 -41 Left 2
SYMATTR Value SINE(0 123 60 0 0 0) SYMATTR InstName V1
SYMBOL ind -736 208 R90
WINDOW 0 5 56 VBottom 2
WINDOW 3 32 56 VTop 2
SYMATTR InstName L2
SYMATTR Value 10µ

SYMATTR SpiceLine Ipk=1.8
SYMBOL res -736 240 R270
WINDOW 0 32 56 VTop 2
WINDOW 3 0 56 VBottom 2
SYMATTR InstName R6
SYMATTR Value 30
SYMBOL res -544 144 R180
WINDOW 0 36 76 Left 2
WINDOW 3 36 40 Left 2
SYMATTR InstName R1
SYMATTR Value 2.4k
SYMBOL res -96 112 R180
WINDOW 0 -43 72 Left 2
WINDOW 3 -74 43 Left 2
SYMATTR InstName R2
SYMATTR Value 18.2k
SYMBOL res -96 16 R180
WINDOW 0 -36 69 Left 2
WINDOW 3 -84 42 Left 2
SYMATTR InstName R3
SYMATTR Value 270k
SYMBOL res -240 16 R180
WINDOW 0 -42 79 Left 2
WINDOW 3 -66 47 Left 2
SYMATTR InstName R4
SYMATTR Value 250k
SYMBOL cap -544 -160 R180
WINDOW 0 24 56 Left 2
WINDOW 3 24 8 Left 2
SYMATTR InstName C2
SYMATTR Value 100n
SYMBOL cap -336 -160 R180
WINDOW 0 24 56 Left 2
WINDOW 3 24 8 Left 2
SYMATTR InstName C3
SYMATTR Value 100n
SYMBOL cap 288 48 R0
SYMATTR InstName C1
SYMATTR Value 47n
SYMBOL ind -192 -224 R270
WINDOW 0 32 56 VTop 2
WINDOW 3 5 56 VBottom 2
SYMATTR InstName L1
SYMATTR Value 10µ
SYMBOL res -336 16 R180
WINDOW 0 36 76 Left 2
WINDOW 3 28 44 Left 1
SYMATTR InstName R5
SYMATTR Value {POT + 1m}
SYMATTR SpiceLine pwr=0.01 SYMBOL Misc\\TRIAC 96 -32 M180 WINDOW 3 48 72 Left 1
SYMATTR Value BTA16-600B
SYMATTR InstName U1
SYMBOL Misc\\DIAC 48 -128 R90

WINDOW 0 0 32 VBottom 2
WINDOW 3 64 32 VTop 2
SYMATTR InstName U2
SYMATTR Value DB3
TEXT 408 72 Left 2 !.tran 0 0.04 0.016 10u
TEXT 408 16 Left 2 !.inc STTRIAC.lib\n.inc STDIAC.lib TEXT 408 -232 Left 2 ;DIAC: DB3\nVbo=13.6V\nIbo=10uA
TEXT 408 -96 Left 2 ;TRIAC: BTA16-600B\nIgt=100mA\nIh=50mA TEXT 408 96 Left 2 ;.step dec param POT 100 250k 30
TEXT -808 160 Left 2 ;Motor
TEXT 8 240 Left 2 ;White Wire
TEXT -832 -256 Left 2 ;Black Wire
TEXT -1008 320 Left 2 ;GND
TEXT 416 168 Left 2 ;.four 50 I(V1)
TEXT 416 192 Left 2 !.meas R1_PWR PARAM 0.84*I(R1)*V(N007,N006)\n.meas R5_PWR PARAM 0.84*I(R5)*V(N006,N003)
TEXT 416 128 Left 2 !.step dec param POT 1 1000 10
RECTANGLE Normal -624 336 -928 176 1

# Appendix II - Packaging

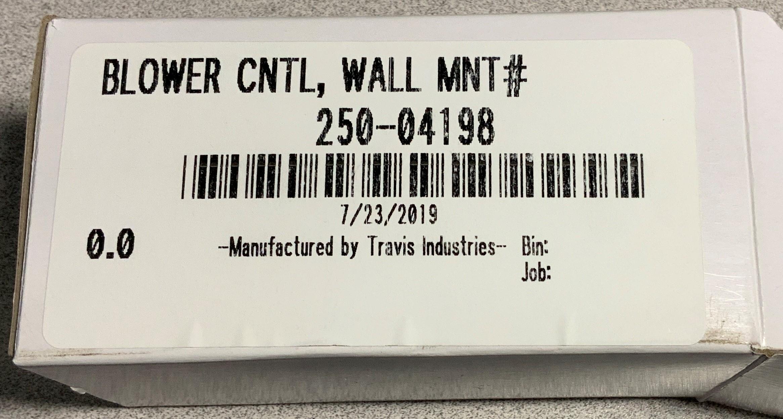
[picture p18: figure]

Figure 21 - YLFC700 Packaging

# Appendix III - Legal Notice

Project license: MIT license

You may use this design freely, although as an unemployed college grad I would appreciate any support, shirts, hats, or a donation to a charity of your wishes. An email to alledgedlyengineering@gmail.com stating that you used this design would be nice to know.

Unless consulted first, I do not agree to be involved with any legal ventures or lawsuits.

By using this project you are agreeing to the risks involved with AC current and altering a UL-listed product to fit your needs. In addition, you agree to not hold me responsible for any injury or result of injury incurred by modifying the YLFC700 unit or my hobbyist solution presented. This project has no affiliations.

I am simply a hobbyist creating a hobbyist project for my personal use.

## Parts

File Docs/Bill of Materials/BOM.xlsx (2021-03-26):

Bill of Materials
Reference | Quantity | Value | Footprint | Datasheet | Other | Part | digikey
C1 | 1 | 47n | Capacitor_THT:C_Rect_L11.5mm_W5.2mm_P10.00mm_MKT | https://content.kemet.com/datasheets/KEM_C1055_HIVOLT_GOLDMAX_300_X7R.pdf | Ceramic Cap, 1kV | C330C473KDR5TA | 399-14748-ND
C2 C3 | 2 | 100n | Capacitor_THT:C_Rect_L11.5mm_W5.2mm_P10.00mm_MKT | https://www.illinoiscapacitor.com/pdf/seriesDocuments/MSR%20series.pdf | 250V | 104MSR400K | 1572-1012-ND
D1 | 1 | DB3 | Diode_THT:D_DO-35_SOD27_P7.62mm_Horizontal | https://www.st.com/content/ccc/resource/technical/document/datasheet/23/5c/f1/97/51/d1/4a/8f/CD00002289.pdf/files/CD00002289.pdf/jcr:content/translations/en.C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 | Ipk=2A, Ibr=15uA, Vbr=30~34V | DB3TG | 497-3134-2-ND
F1 | 1 | Fuse | my_lib:FUSC6125X279N | https://belfuse.com/resources/datasheets/circuitprotection/ds-cp-0679l-series.pdf | 4 Amp | 0679L4000-05‎ | 507-1993-1-ND‎
H1 H2 | 2 | MountingHole | MountingHole:MountingHole_3mm | ~
H3 | 1 | MountingHole | MountingHole:MountingHole_5mm | ~
J1 | 1 | BlackWire | my_lib:Pin_D1.7mm | ~
J3 | 1 | WhiteWire | my_lib:Pin_D1.7mm | ~
L1 | 1 | L_Core_Ferrite | my_lib:TRIAC_Choke | ~
Q1 | 1 | BTA16-600B | Connector_PinSocket_2.54mm:PinSocket_1x03_P2.54mm_Vertical | https://www.st.com/resource/en/datasheet/bta16.pdf | 16A, 600V, Vgt=1.3V, Igt=50mA | BTA16-600BRG | 497-2397-5-ND
R1 | 1 | 2.4k | Resistor_THT:R_Axial_DIN0207_L6.3mm_D2.5mm_P10.16mm_Horizontal | ~ | 2W
R2 | 1 | 270k | Resistor_SMD:R_1206_3216Metric_Pad1.30x1.75mm_HandSolder | https://www.te.com/commerce/DocumentDelivery/DDEController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 | 1% 1W | CRGP1206F270K‎ | ‎A130567CT-ND‎
R3 | 1 | 18k | Resistor_SMD:R_1206_3216Metric_Pad1.30x1.75mm_HandSolder | https://www.te.com/commerce/DocumentDelivery/DDEController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 | 1% 1/2W | CRGP1206F18K‎ | ‎A130553CT-ND‎
R4 | 1 | 240k | Resistor_SMD:R_1206_3216Metric_Pad1.30x1.75mm_HandSolder | https://d1d2qsbl8m0m72.cloudfront.net/en/products/databook/datasheet/passive/resistor/chip_resistor/esr-e.pdf | 5% 1/2W | ‎ESR18EZPJ244‎ | RHM240KICT-ND‎
R5 | 1 | 24 | Resistor_SMD:R_2512_6332Metric_Pad1.40x3.35mm_HandSolder | https://www.seielect.com/catalog/sei-rmcf_rmcp.pdf | 5% 1W | RMCF2512JT24R0 | RMCF2512JT24R0CT-ND
RV1 | 1 | R_POT_10_to_300k | my_lib:91A1A-B28-A22L-Bottom | https://www.bourns.com/docs/Product-Datasheets/91_95.pdf | 2W 0.2 to 250k | 91A1A-B28-A22L‎ | 91A1A-B28-A22L-ND
SW1 | 1 | SW_DIP_x01 | my_lib:GRS-2011-2055 | https://media.digikey.com/pdf/Data%20Sheets/CW%20Industries%20PDFs/GRSV-4011-0123_THRU_-0127_Dwg.pdf | 13A 125VAC | ‎GRSV-4011-0126‎ | ‎CWI487-ND‎

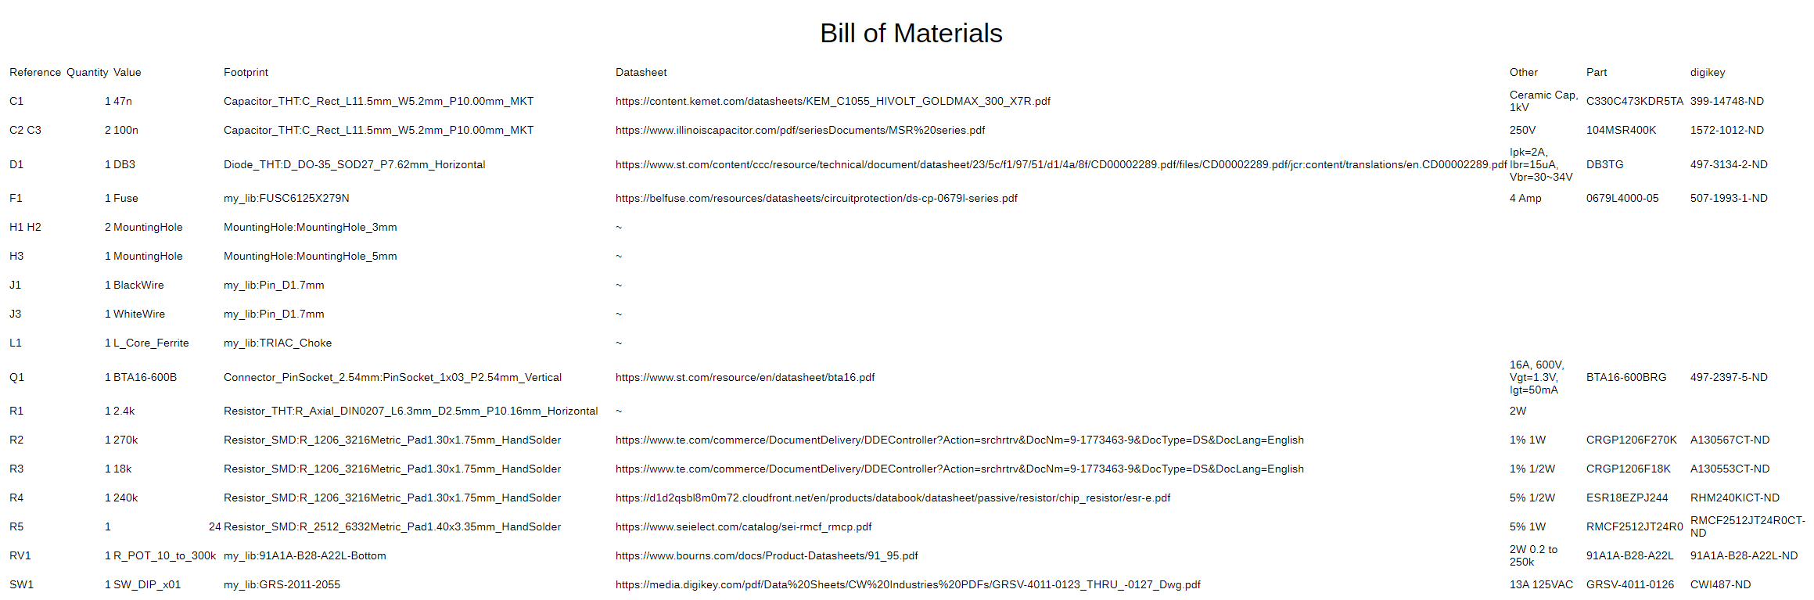
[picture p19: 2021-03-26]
Docs/Bill of Materials/BOM.PNG

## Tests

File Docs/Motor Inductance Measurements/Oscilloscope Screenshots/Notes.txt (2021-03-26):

Channel 1 - Placed on Motor Lead to Main Neutral
Channel 2 - Placed on Output of TRIAC to Motor

Images:
SDS1 - FFT CH3, Windowing: Rectangle, Center Freq: 0 Hz, Hz/Div: 20KHz
SDS2 - FFT CH1, Windowing: Hamming, Center Freq: 60 Hz, Hz/Div: 500Hz
SDS3 - FFT CH1, Windowing: Hamming, Center Freq: 60 Hz, Hz/Div: 500Hz
SDS4 - FFT CH3, Windowing: Hamming, Center Freq: 60 Hz, Hz/Div: 500Hz
SDS5 - General Image of Channels
SDS6 - Motor on Highest Speed from TRIAC
SDS7 - Motor on Lowest Speed from TRIAC
SDS8 - General Image of Channels
SDS9 - Same as SDS8, but with Measurements displayed

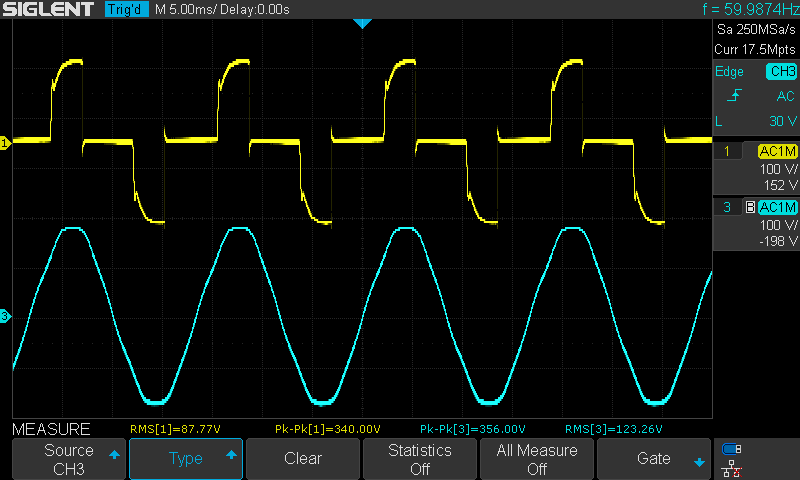
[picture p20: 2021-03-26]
Docs/Motor Inductance Measurements/Oscilloscope Screenshots/SDS00009.png

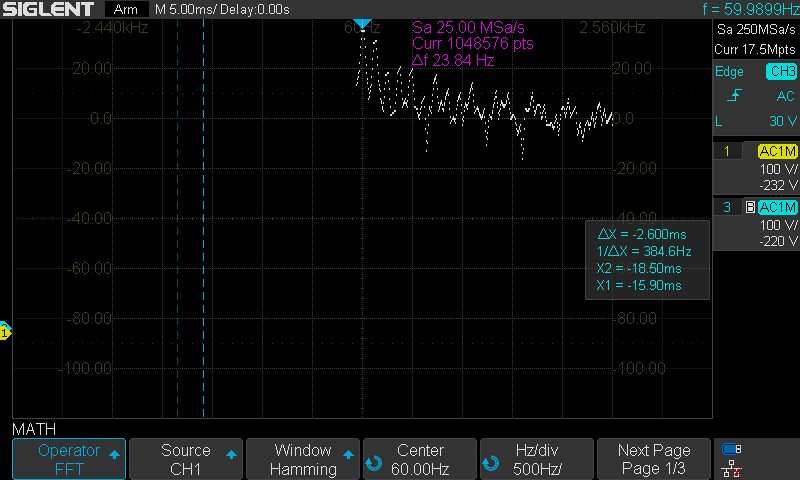
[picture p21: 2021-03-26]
Docs/Motor Inductance Measurements/Oscilloscope Screenshots/SDS00003.png

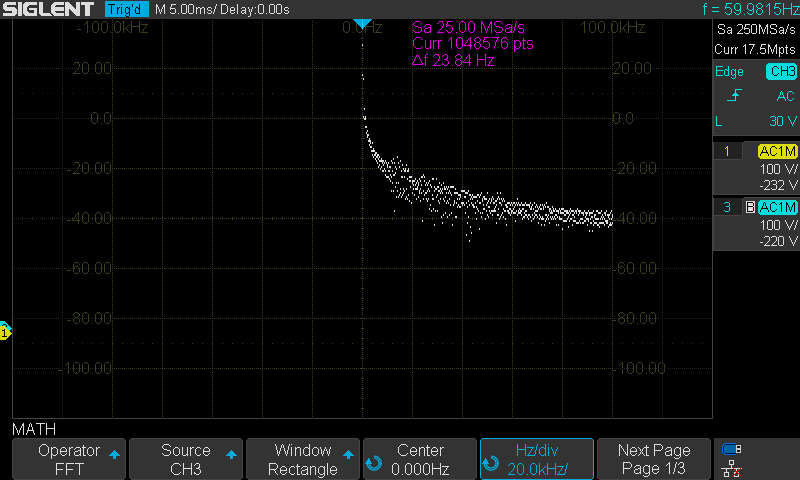
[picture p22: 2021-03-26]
Docs/Motor Inductance Measurements/Oscilloscope Screenshots/SDS00001.png

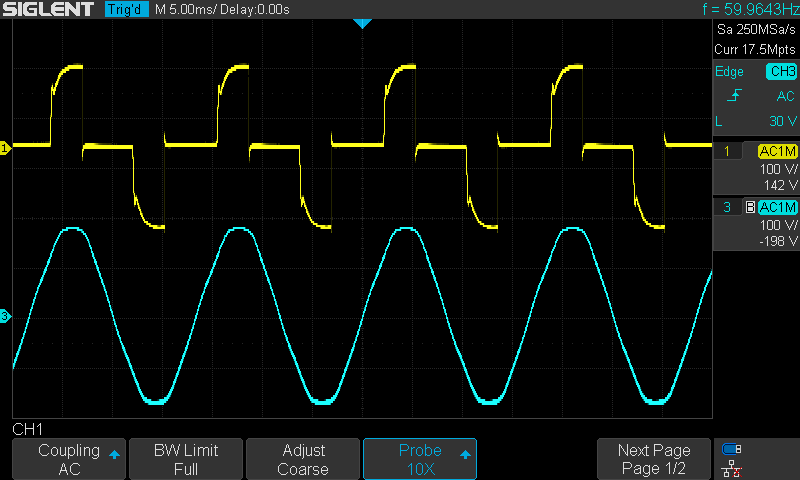
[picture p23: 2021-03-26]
Docs/Motor Inductance Measurements/Oscilloscope Screenshots/SDS00008.png

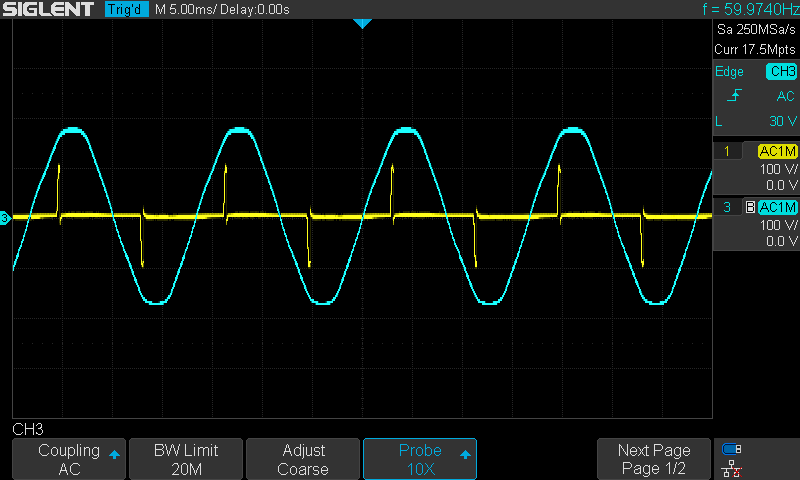
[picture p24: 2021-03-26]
Docs/Motor Inductance Measurements/Oscilloscope Screenshots/SDS00006.png

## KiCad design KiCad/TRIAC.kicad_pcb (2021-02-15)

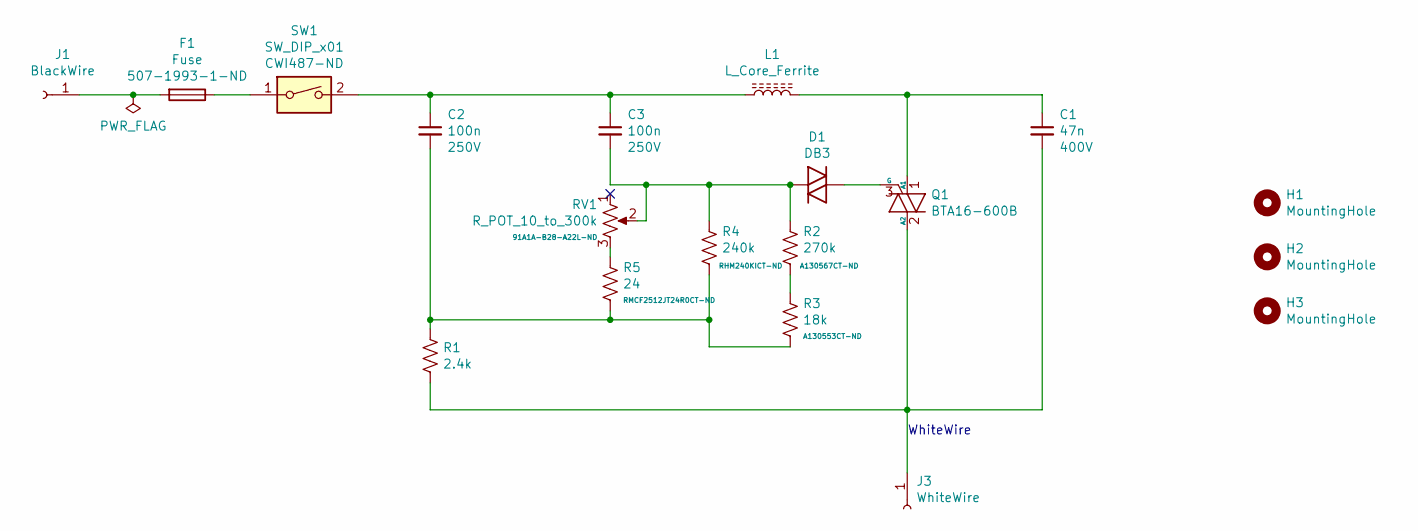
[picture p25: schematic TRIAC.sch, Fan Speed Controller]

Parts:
C1: 47n; C_Rect_L11.5mm_W5.2mm_P10.00mm_MKT
C2, C3: 100n; C_Rect_L11.5mm_W5.2mm_P10.00mm_MKT
D1: DB3; D_DO-35_SOD27_P7.62mm_Horizontal
F1: Fuse; FUSC6125X279N; Part 0679L4000-05‎; digikey 507-1993-1-ND‎
H1, H2: MountingHole; MountingHole_3mm
H3: MountingHole; MountingHole_5mm
J1: BlackWire; Pin_D1.7mm
J3: WhiteWire; Pin_D1.7mm
L1: L_Core_Ferrite; TRIAC_Choke
Q1: BTA16-600B; PinSocket_1x03_P2.54mm_Vertical; digikey 497-2397-5-ND
R1: 2.4k; R_Axial_DIN0207_L6.3mm_D2.5mm_P10.16mm_Horizontal
R2: 270k; R_1206_3216Metric_Pad1.30x1.75mm_HandSolder; Part CRGP1206F270K‎; digikey ‎A130567CT-ND‎
R3: 18k; R_1206_3216Metric_Pad1.30x1.75mm_HandSolder; Part CRGP1206F18K‎; digikey ‎A130553CT-ND‎
R4: 240k; R_1206_3216Metric_Pad1.30x1.75mm_HandSolder; Part ‎ESR18EZPJ244‎; digikey RHM240KICT-ND‎
R5: 24; R_2512_6332Metric_Pad1.40x3.35mm_HandSolder; Part RMCF2512JT24R0; digikey RMCF2512JT24R0CT-ND
RV1: R_POT_10_to_300k; 91A1A-B28-A22L-Bottom; Part 91A1A-B28-A22L‎; digikey 91A1A-B28-A22L-ND
SW1: SW_DIP_x01; GRS-2011-2055; Part ‎GRSV-4011-0126‎; digikey ‎CWI487-ND‎

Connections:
unnamed: C1.1, L1.2, Q1.1 (A1)
unnamed: C1.2, J3.1, Q1.2 (A2), R1.2
unnamed: C2.1, C3.1, L1.1, SW1.2
unnamed: C2.2, R1.1, R3.2, R4.2, R5.2
unnamed: C3.2, D1.1 (K), R2.1, R4.1, RV1.2
unnamed: D1.2 (A), Q1.3 (G)
unnamed: F1.1, SW1.1
unnamed: F1.2, J1.1
unnamed: R2.2, R3.1
unnamed: R5.1, RV1.3

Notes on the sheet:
WhiteWire

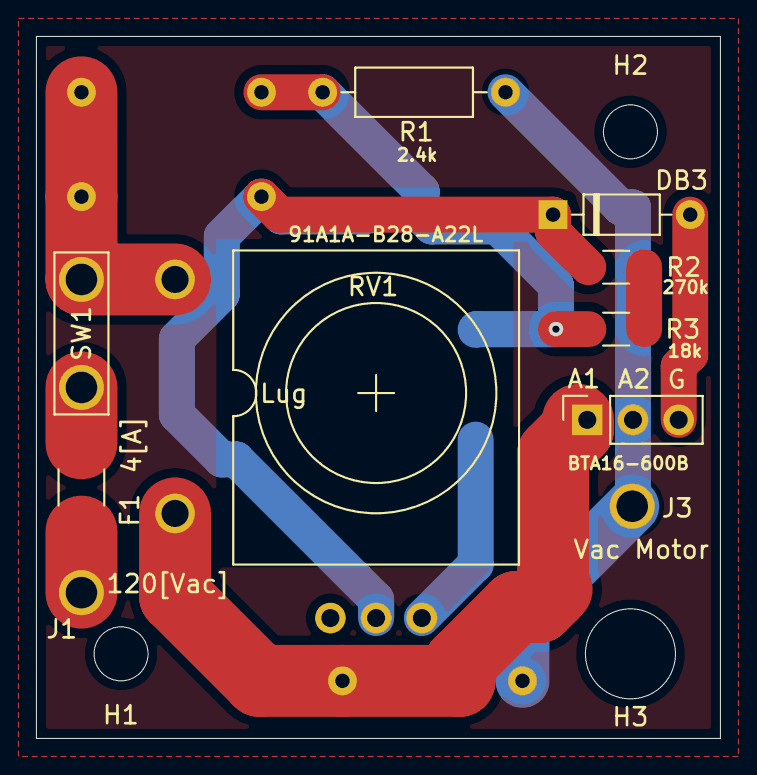
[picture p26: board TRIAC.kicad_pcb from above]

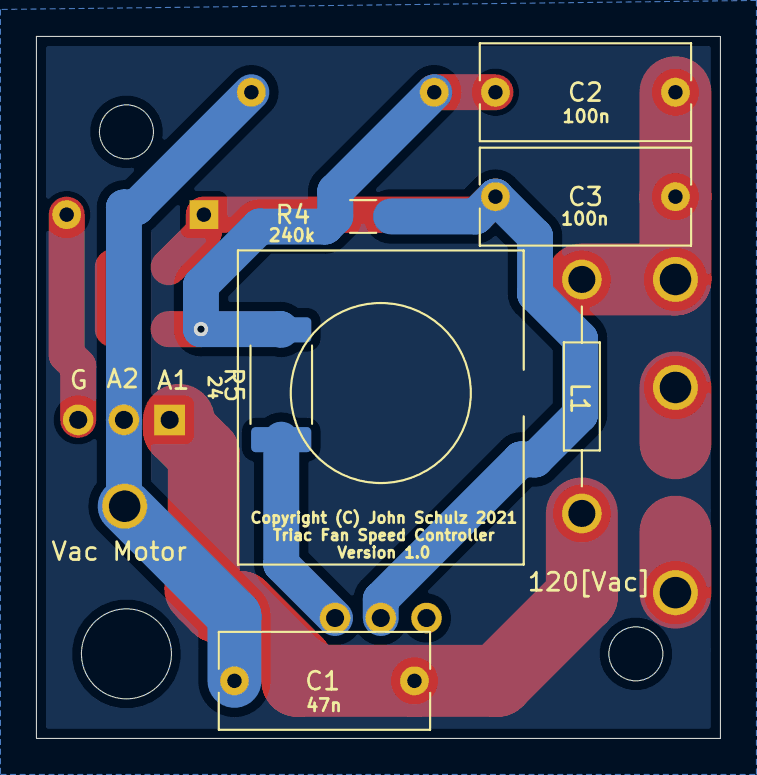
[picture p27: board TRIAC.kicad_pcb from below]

Board: 2 copper layers, 38.0 x 39.0 mm, 19 parts (6 on the bottom side), 10 nets.

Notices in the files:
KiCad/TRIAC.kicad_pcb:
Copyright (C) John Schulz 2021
